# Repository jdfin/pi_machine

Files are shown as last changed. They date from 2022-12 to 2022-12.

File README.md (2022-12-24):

# Pi Machine

Pi Machine prints pi, for as long as you let it run. It was inspired by a couple of projects covered at [Hackaday](https://hackaday.com/): the [Pi Spigot](https://hackaday.com/2021/04/06/raspberry-pi-spigot-puts-digits-of-pi-on-tap/) and [Happy Pi Day 2022](https://hackaday.com/2022/03/15/simple-arduino-build-lets-you-keep-an-eye-on-pi/). The latter's [project page](https://www.linkedin.com/pulse/happy-%25CF%2580-day-2022-cristiano-monteiro) describes how it uses [Xavier Gourdon's](http://numbers.computation.free.fr/Constants/constants.html) [nth-digit algorithm](http://numbers.computation.free.fr/Constants/Algorithms/nthdigit.html) to compute and display digits directly (i.e. compute the nth digit without (necessarily) having computed all the digits before it).

The difference between those and this Pi Machine is that this one prints digits on a thermal printer, and contains logic and hardware (paper-change, power-fail) that in theory lets it run forever. The software herein can be configured to run without any special hardware (other than an Arduino-capable board), but in that case it will just print digits to the serial console.

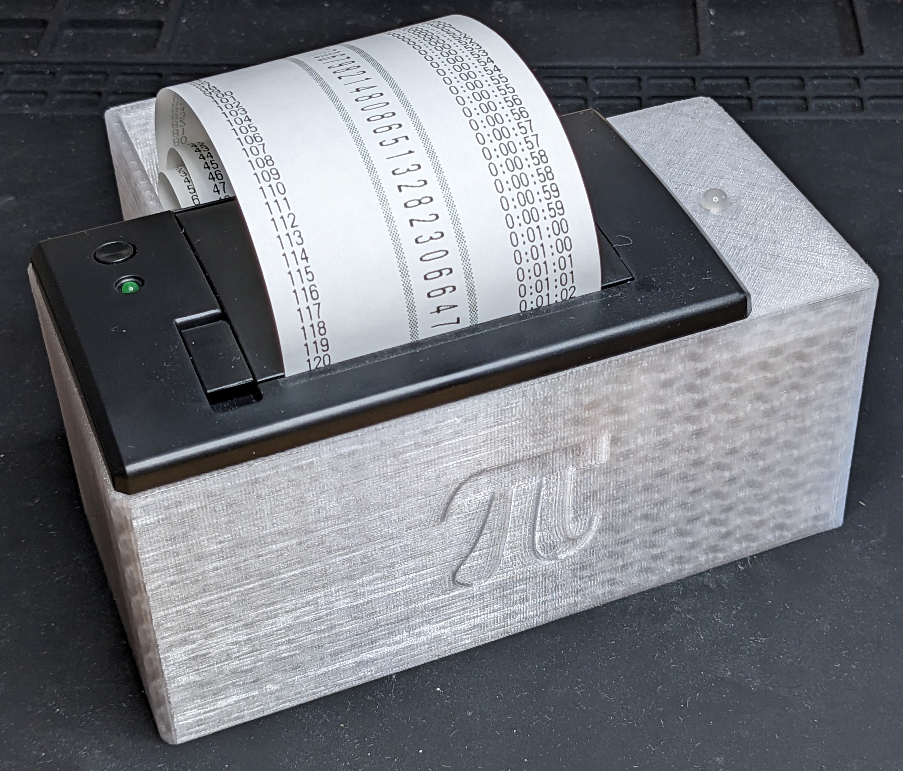
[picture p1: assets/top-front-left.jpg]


The complete (as-built) Pi Machine uses:
* [Adafruit Feather M4 Express](https://www.adafruit.com/product/3857). Minimizing the hardware (how slow can you go) might point to an M0 board, but I had some of the M4 Express "in stock". I first tried on a [DF Robot Beetle](https://www.dfrobot.com/product-1075.html), but that doesn't (easily, out-of-the-box) support 64-bit doubles, and 32-bit doubles lead to a failure at about digit 768, possibly due to the six nines in a row there. It works on an M0 ([Seeeduino XIAO](https://www.seeedstudio.com/Seeeduino-XIAO-Arduino-Microcontroller-SAMD21-Cortex-M0+-p-4426.html) or [Adafruit QT Py - SAMD21](https://www.adafruit.com/product/4600), but I wanted a battery charger, which led me to the [Feather](https://www.adafruit.com/category/943). The [M0 Express](https://www.adafruit.com/product/3403) would be the "lowest-end" hardware, but I had a few of the M4 Express, so the Pi Machine is twice as fast as it could have been. It also runs on a [PJRC Teensy 4.0](https://www.pjrc.com/store/teensy40.html), but 600 MHz and hardware floating point kinda spoils the fun. And I wanted the charger.
* [Thermal Printer](https://www.adafruit.com/product/597). This link is to the printer at Adafruit, but I think you can get the same printer from a number of places. I think the firmware can (will) be different depending on where you get it - I got one of the Adafruit printers via Mouser, and one from Adafruit directly, and they are different in some user-apparent ways. I ended up not using the Adafruit library for it, just because I was innit enough trying to figure it out that I used my own stuff (so the library in here is not suitable for general purpose use). One of the smaller printers would work (after dealing with firmware differences), but the larger paper capacity of the "Mini" seems nice.
* [LiPo](https://www.adafruit.com/product/4236). The purpose of the LiPo is to let you unplug the Pi Machine to move it and not have it start over. I briefly tried making it so it would run from the battery, but it's hard getting enough power to the thermal printer and clean power to the microprocessor such that light printing and brownouts are not an issue. So it charges while plugged in, and when Pi Machine detects it has been unplugged, it just stops printing and waits to be plugged in again. I don't know how long the battery will last. At one point I measured the current draw of just the M4 Express blinking the LED and decided 420 mAh was enough, but don't have or recall the details.
* [RGB LED](https://www.adafruit.com/product/302). This one is has the diffused lens, which I like. I just picked resistors that gave a good brightness, and R, G, and B are just on or off (no pwmmin').
* [Power Jack](https://www.adafruit.com/product/610) and [Power Supply](https://www.adafruit.com/product/276).
* [Switch](https://www.mouser.com/ProductDetail/979-1901.1102). Any switch will do, but this one fits the 3D printed chassis.
* Resistors for power detection (2 x 100K) and the RGB LED (1.5K, 5.1K, 5.1K).
* Connectors for anything you don't want soldered together. The printer is JST-XH (2.5mm), and I used JST-PH (compatible) elsewhere (2.0mm). For the printer I used bits from one of those JST-XH "kits" off Amazon, and for the rest (JST-PH) I use the connectors-with-tails from Adafruit (e.g. [this](https://www.adafruit.com/product/261) and [this](https://www.adafruit.com/product/3814)).
* There is no PCB; the voltage divider fits on the M4 Express, and the LED resistors are hanging in space.

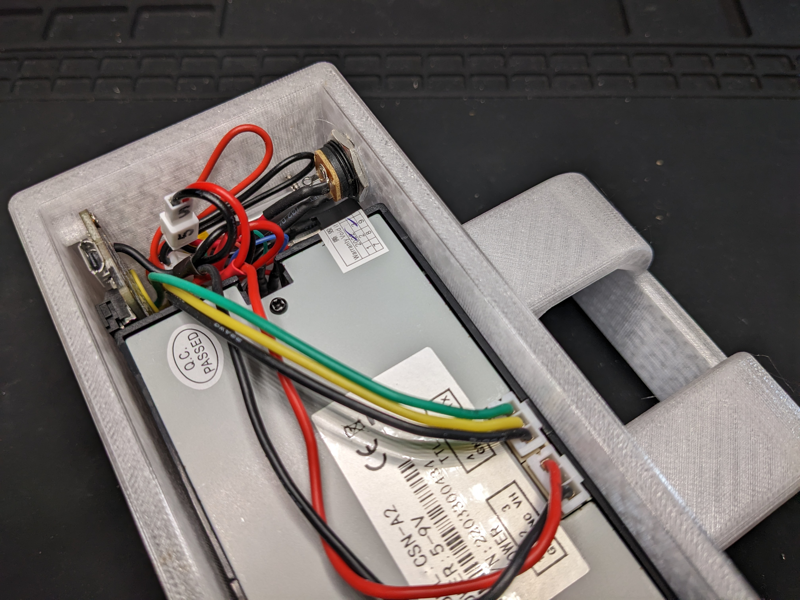
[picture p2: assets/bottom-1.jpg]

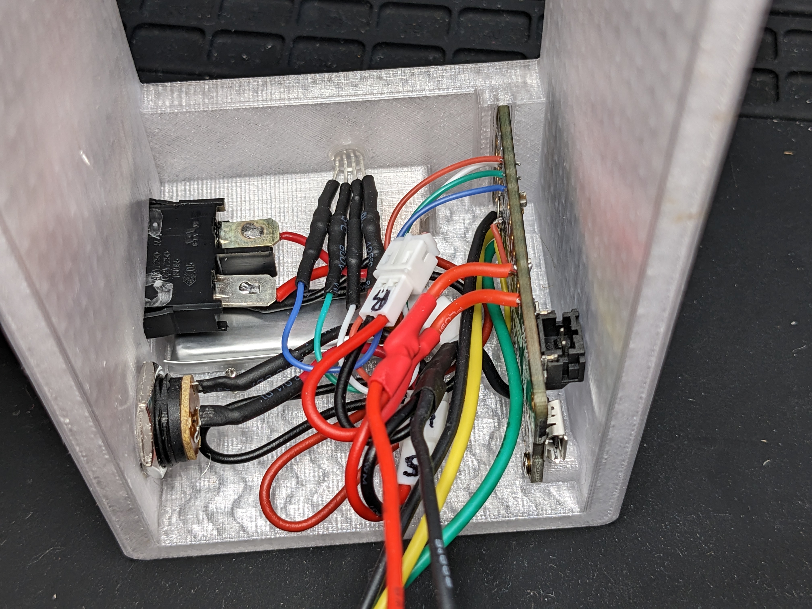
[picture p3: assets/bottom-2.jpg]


## Code

It's all Arduino. I use arduino-cli these days (not the IDE, new or old). You kinda have to know a bit about it already, but here are some bits about how I use it. I use windows, so these are all "cmd.exe" (old-style) batch files. CLI version 0.29 was newest when I did this.
* [Get and install arduino-cli](https://arduino.github.io/arduino-cli/). Drop the executable right there in the "Arduino" directory.
* Edit ac-init.bat according to what you plan to use (it is set for Feather M4 Express as committed). I don't know how to easily find the FQBN for an arbitrary board; running the IDE, enabling verbose output, and plodding through the build output might work.
* Run ac-init.bat. It will get some stuff from Arduino and Adafruit, then create a batch file for the board, namely "ac-feather_m4.bat".
* Run the board batch file. All it does is set an environment variable with the FQBN so the other scripts know how to build/load.
* Run ac-list.bat to look for and list the boards plugged in (so you can see the com port).
* Run ac-build.bat to build and optionally download to the board.
* If needed, run ac-serial.bat to connect to the serial console.

### Running with Only the CPU

No printer, no battery, no power plug. Just a board hanging off USB. This should work with a Feather M4 Express, or with slight modifications to the batch files, an M0 Express, QT Py M0, Xiao, or something of that sort. It just needs 64-bit doubles. It'll compile and run with 32-bit doubles, but the output won't be right.

Edit 2022-11-17_PiMachine.ino:
* WAIT_CONSOLE 1
* PRINT_DIGITS 0
* CHECK_PAPER 0
* CHECK_POWER 0

ac-build 2022-11-17_PiMachine COM*N*

It should build and download.

ac-serial COM*N*

It should connect to the serial port and you should get digit spewage.

### The Software

Stuff shared between sketches is in libraries/PiMachine. That's just how I happen to do it; I can have several test sketches or other variations using the same shared files.
* printer.cpp, printer.h - just enough for this, not for general usage. There might be things in here that don't work in the Adafruit library; I should have fixed and PR'd but didn't. I wouldn't be able to regression test for other firmware versions anyway.
* pidec.cpp, pidec.h - the original source for the nth-digit algorithm, first reformatted (sorry), then converted to run as a subroutine as required for testing and the Pi Machine.
* millis64.cpp, millis64.h - since the idea is to allow it to run for years (ha ha), we need 64 bit milliseconds.
* chrono.cpp, chrono.h - there was a time when I learned and understood std::chrono, and ended up liking it, mostly, iirc. I added this tiny bit of that in response to various subtle problems around pausing and restarting printing (paper change, power unplugged). It's the distinction between time stamps and durations that seems satisfying.
* Sketches - tests for various parts, then the main Pi Machine is in 2022-11-17_PiMachine.
  - Dealing with the printer is split between print_digit() and printer.cpp mentioned previously. Trying to get a digit number, digit, and timestamp on the same line is a little funky, figuring out what that settings mean when text is sideways and such. I think it is the mixing of sideways and not-sideways that causes differences between firmware versions to show up. E.g. one Pi Machine successfully bolds the sideways digit, and one does not.
  
I don't actually understand how the algorithm works, but I've run it to tens of thousands of digits on a Teensy 4.0 and I don't think I've broken it.

### More Hardware

Schematic notes:
* "5V Power Jack" is the 2 amp wall-wart. If this is connected, see POWER NOTE below before plugging in USB or you might be connecting the wal-wart right across your computer's USB port.
* "Switched Battery" is the LiPo, with a switch inline with the + side. The switch is to be able to turn the thing completely off. When running, the switch is normally on so the battery charges. Then when you unplug power, if the switch is on, it sits and waits patiently and does not start all over. If I end up running this thing for a year, I'll probably wish I had put more thought into how the power works.
* 3V3 to the LED comes from the regulator on the Feather. The LED resistors are hanging off the LED, then wired to the CPU board.
* The 100K divider is so the CPU can detect when power is unplugged. It doesn't drop to zero; it drifts down to  3-point-something; enough to detect it. Smaller divider resistors might get it lower, but I did not try. These resistors are mounted to the "Express" area of the CPU board.
* "Printer Serial" is three wires to the JST-XH on the bottom of the printer, and "Printer Power" is two wires going to the other 3-pin JST-XH on the bottom of the printer.

**POWER NOTE:** If the board is powered by a 5V supply you need to **think about** whether you can just plug in USB or not. For the Feather M4 Express, the Pi Machine connects the 5V supply to VUSB, so you should probably not plug in USB at the same time (lest your computer and the wall-wart argue over who can supply more current). I have a USB cable where I cut the +5 wire just for this purpose; you can power with the wall-wart, and plug in the USB cable that just has D+, D-, and GND, and it works nicely.

The chassis was all done in Fusion 360 and printed on a Prusa i3 MK3S+ with PETG.

## Tiny Pi Machine

My grandson likes to push buttons and make things whirr, so I built the Tiny Pi Machine with the "[Nano](https://www.adafruit.com/product/2752)" printer that I ended up not using for the Pi Machine. It does not compute pi; it just prints it as long as the button is down, then starts over and does it again the next time you push the button. Not terribly exciting unless you are 3; then it's easy to go through rolls and rolls of paper.

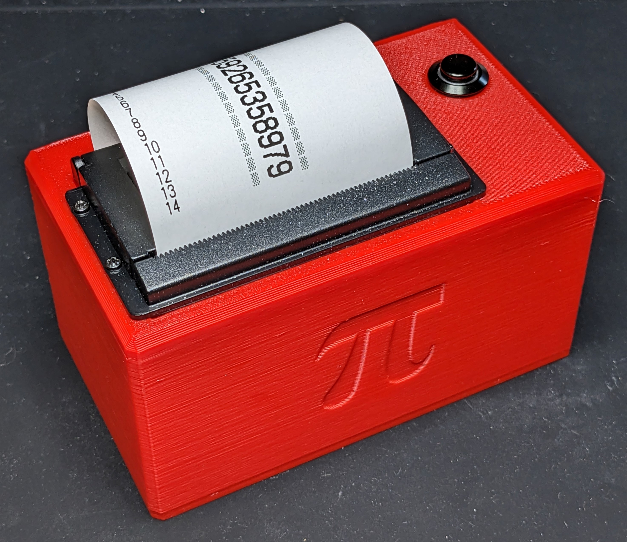
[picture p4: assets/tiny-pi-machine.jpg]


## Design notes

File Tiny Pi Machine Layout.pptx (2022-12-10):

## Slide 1

VIN

B+

ON

VOUT

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
VOUT

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
CTRL

A0

A1

A2

5V

TOP

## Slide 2

VIN

B+

ON

VOUT

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
VOUT

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
CTRL

A0

A1

A2

5V

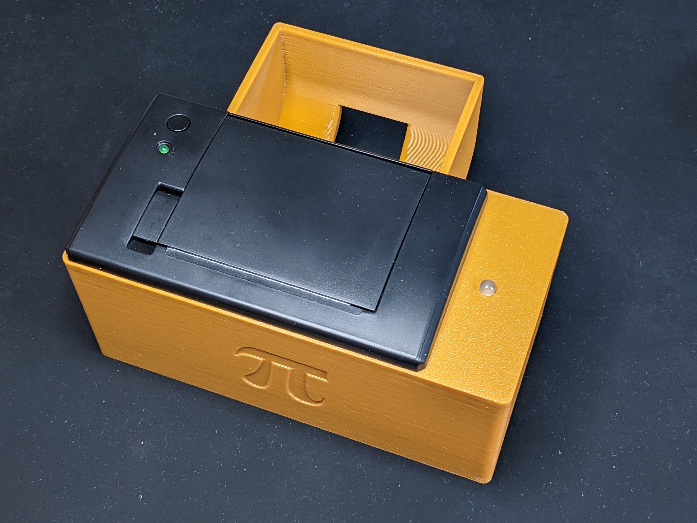
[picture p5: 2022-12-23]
assets/top-front-right.jpg

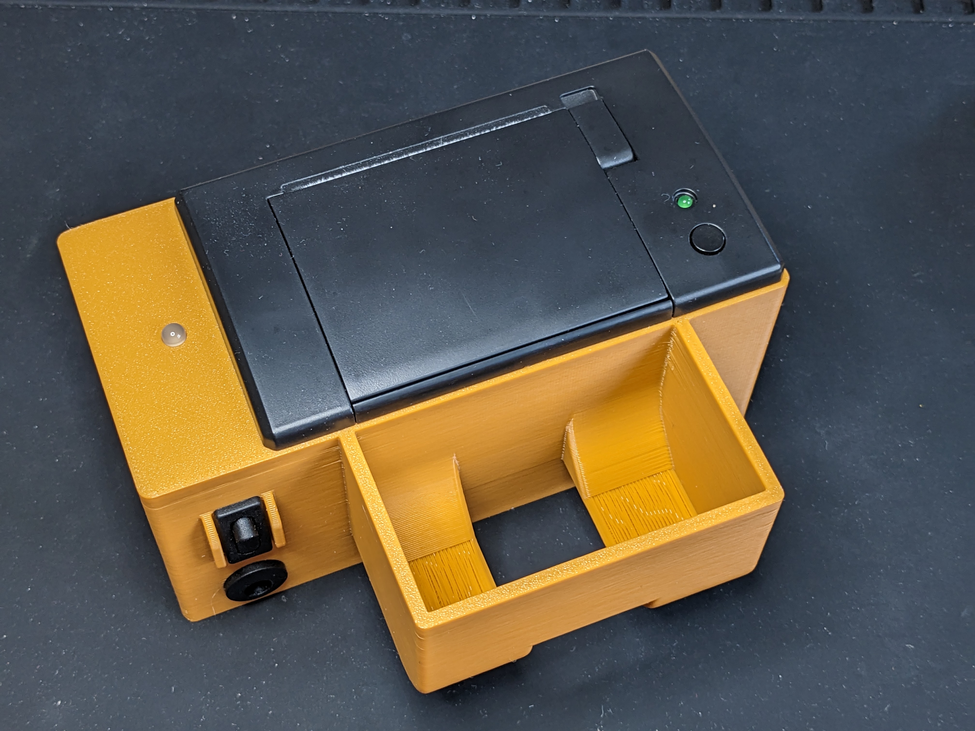
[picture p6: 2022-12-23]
assets/top-rear.jpg

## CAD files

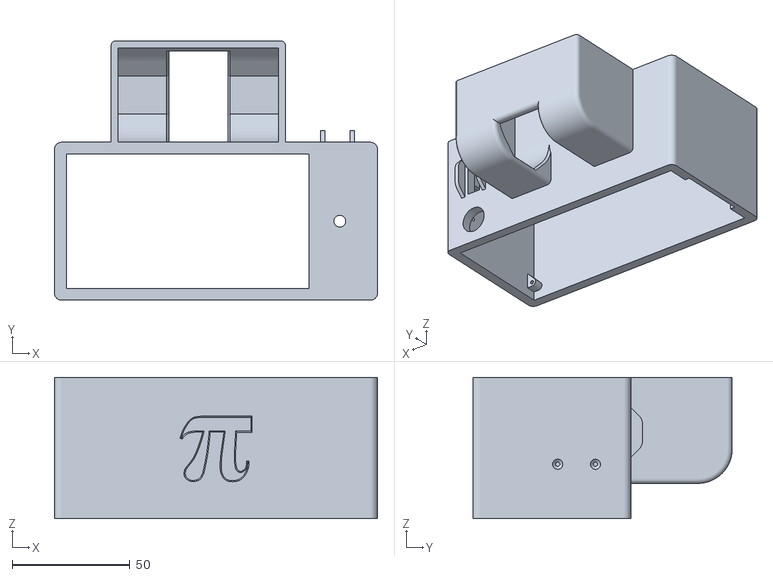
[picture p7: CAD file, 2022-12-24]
pi_machine.stl
137.0 x 110.0 x 60.0

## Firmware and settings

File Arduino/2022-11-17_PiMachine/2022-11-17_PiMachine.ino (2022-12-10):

// PiMachine

#include <Arduino.h>
#include <string.h>
#include <stdio.h>
#include <pidec.h>
#include <rgb.h>
#include <printer.h>
#include <chrono.h>

// if 1, wait for serial (usb) console before starting
#define WAIT_CONSOLE 0

// if 1, print to real printer in addition to console
#define PRINT_DIGITS 1

// if 1, check for paper out (can do this without printing digits)
#define CHECK_PAPER 1

// if 1, switch on GPIO simulates paper out
#define CHECK_PAPER_FAKE 0

static const int paper_fake_pin = 10;
static const int paper_fake_yes = 1; // gpio when "paper is present"

// if 1, check power and pause when not present
// (requires divider connected to a/d pin)
#define CHECK_POWER 1

// Minimum number of milliseconds per digit printed.
// 250 seems to be about the fastest, slower for debugging.
#if PRINT_DIGITS
static const Interval print_interval(500);
#else
static const Interval print_interval(0);
#endif

// 19200 for the Mini, 9600 for the Nano
static const int printer_baud = 19200;

static Printer printer(Serial1);

static const int red_pin = 5;
static const int green_pin = 6;
static const int blue_pin = 9;
static Rgb led(red_pin, green_pin, blue_pin);


// The start time is advanced when waiting for power or paper.
static Time start_time;

// In the program, first digit after the decimal (the 1) is digit zero
// (that is dictated by DigitsOfPi).
//
// In the printout, the initial '3' is digit zero, so the printout uses
// digit_num + 1.
//
// digit_num: -4 and -3 are spaces, -2 is the '3', -1 is the '.', then
//            0.. are the digits after the decimal point
static const int32_t digit_num_start = -4;
static int32_t digit_num = digit_num_start;


// How long it took to calculate the most recent digit.
// loop() sets this and print_digit() uses it.
static Interval digit_interval;


#if CHECK_PAPER || CHECK_PAPER_FAKE

// return true if the printer claims to have paper, false otherwise
static bool check_paper()
{
#if CHECK_PAPER_FAKE
  return (digitalRead(paper_fake_pin) == paper_fake_yes);
#else
  return printer.paper();
#endif
}

#endif // CHECK_PAPER || CHECK_PAPER_FAKE


// If paper is detected, return true immediately.
// If paper is not detected, wait for it to be detected continuously
// for 10 seconds, then return false.
// Logic is similar to power_wait, but in here we also allow for power
// disappearing (i.e. run out of paper, unplug it to move it or something).
static bool paper_wait()
{

#if CHECK_PAPER || CHECK_PAPER_FAKE

  if (check_paper())
    return true;

  Serial.println("paper out");

  // Time we started waiting for more paper. This is used to adjust the global
  // start_time so it doesn't include paper-out time.
  const Time wait_start;

  // Need to see paper for 10 seconds before continuing.
  const Interval wait_timeout(10000);

  // Last time paper was detected as "out".
  Time paper_out;

  while ((Time::now() - paper_out) < wait_timeout) {

    if (!power_wait()) {
      // power went away, then came back
      paper_out = Time::now();
    }

    if (check_paper()) {
      // solid red means we see paper, waiting for 10 seconds
      led.set(Rgb::Red);
    } else {
      // winking red means we don't see paper
      led.pattern(Rgb::Red, 10, Rgb::Off, 990);
      paper_out = Time::now();
    }

    led.loop(); // handle blinking

    yield(); // could be in this while loop for a long time

  } // while

  // Adjust start_time as if we didn't have to wait.
  start_time += (Time::now() - wait_start);

  // Back up 30 digits after paper out. A nice clean end-of-paper only needs
  // a few digits of backing up (4 or 5 might do), but sometimes the end of
  // the roll is folded back on itself and a couple of inches at the end
  // don't print because it's trying to print on the back of the paper.
  // We're printing about 8.5 lines per inch.
  digit_num -= 30;
  if (digit_num < digit_num_start)
    digit_num = digit_num_start;

  Serial.println("paper okay");

  return false;

#else // CHECK_PAPER(_FAKE)

  return true;

#endif // CHECK_PAPER(_FAKE)

} // paper_wait


// return true if 5V supply is present, false otherwise
static bool check_power()
{

#if CHECK_POWER

  // VUSB is 5.0V when plugged in, and is about 3.3V when not plugged in.
  // The pin is half that. Set threshold for halfway between 5.0 and 3.3.
  // Halfway between 3.3 and 5.0 is 4.15V.
  // Pin is half that, or 2.075V.
  // ADC reading is 1024 at 3.3V, so ADC threshold is 644.
  const int v_thresh = 644;
  int v = analogRead(2);

  return (v >= v_thresh);

#else // CHECK_POWER

  return true;

#endif // CHECK_POWER

} // check_power


static bool power_wait()
{

  if (check_power())
    return true;

  Serial.println("power out");

  // Wait to be plugged in for at least 1 sec, then return false.
  // The delay is to let the printer boot up.
  // Returning false prevents the just-calculated digit from being printed.

  const Time wait_start;

  const Interval wait_timeout(1000); // 1 second

  // last time power was seen low
  Time power_low;

  while ((Time::now() - power_low) < wait_timeout) {

    if (check_power()) {
      // solid blue means we see 5V power, waiting 1 second
      led.set(Rgb::Blue);
    } else {
      // winking blue means we don't see 5V power
      led.pattern(Rgb::Blue, 10, Rgb::Off, 990);
      power_low = Time::now();
    }

    led.loop(); // handle blinking

    yield(); // could be in this while loop for hours

  } // while

  // Adjust start_time as if we didn't have to wait.
  start_time += (Time::now() - wait_start);

  // Back up three digits after power outage; really only the previous one
  // might be chopped off, but maybe there's some other case where more than
  // one might be lost, and losing a digit would be most terrible.
  digit_num -= 3;
  if (digit_num < digit_num_start)
    digit_num = digit_num_start;

  Serial.println("power okay");

  return false;

} // power_wait


// print a digit (paper and power already checked)
// 
static void print_digit(char digit)
{
  // Limit print rate so we don't queue up lines in the receive buffer,
  // which breaks paper-out handling. This is different from worrying
  // about overrunning the receive buffer; we basically want to know a
  // digit is on the paper before we try to print another one.
  static Time last_print_time;
  while ((Time::now() - last_print_time) < print_interval)
    delay(1);
  last_print_time = Time::now();

  // timestamp that will print with digit
  uint32_t h, m, s, ms;
  (last_print_time - start_time).hmsm(h, m, s, ms);

  // digit number to print
  int32_t pr_digit_num;
  if (digit_num == -2)
    pr_digit_num = 0; // initial '3'
  else
    pr_digit_num = digit_num + 1;

  // large font is 12 pixels wide x 24 pixels high

  // rotated and doubled digit is 48 pixels wide
  // digit should be centered on 384/2 = 192, so should print at
  // 192 - (48 / 2) = 168

  // line will be:
  // digit number: 12 chars @ 12 pixels = 144 pixels
  // border:        2 chars @ 12 pixels =  24 pixels
  // digit:         1 char  @ 48 pixels =  48 pixels
  // border:        2 chars @ 12 pixels =  24 pixels
  // timestamp:    12 chars @ 12 pixels = 144 pixels
  // total:                               384 pixels

  char buf[50];

  // only print number and timestamp if digit is 0..9
  if ('0' <= digit && digit <= '9')
    sprintf(buf, "%-12ld| %c |%6lu:%02lu:%02lu", pr_digit_num, digit, h, m, s);
  else
    sprintf(buf, "            | %c |            ", digit);
  Serial.print(buf);

  sprintf(buf, "%9lld", digit_interval.ms());
  Serial.print(buf);

  Serial.println();

#if PRINT_DIGITS

  // digit number
  if ('0' <= digit && digit <= '9')
    sprintf(buf, "%-12ld", pr_digit_num); // 12 chars left-justified
  else
    strcpy(buf, "            "); // 12 chars

  printer.rotate(false);
  printer.mode(Printer::Modes::FontLarge);
  printer.print(buf);
  printer.print(0xb2); // gray box
  printer.print(' ');

  // digit
  printer.rotate(true);
  printer.mode(Printer::Modes::FontLarge | Printer::Modes::BoldOn |
               Printer::Modes::Height2x | Printer::Modes::Width2x);
  printer.print(digit);

  // Timestamp. This will run up against the digit in 11 years, then
  // do something uglier in 114 years.
  printer.rotate(false);
  printer.mode(Printer::Modes::FontLarge);
  printer.print(' ');
  printer.print(0xb2); // gray box
  if ('0' <= digit && digit <= '9') {
    sprintf(buf, "%6lu:%02lu:%02lu", h, m, s); // 12 chars right-justified
    printer.print(buf);
  }

  printer.line_space(0);  // lines as close together as possible
  printer.flush();        // print buffered data and advance paper

  printer.mode(); // defaults

#endif // PRINT_DIGITS

} // print_digit


void setup()
{
  led.begin();

  led.set(Rgb::White);

  Serial.begin(115200);

#if WAIT_CONSOLE
  while (!Serial)
    ;
  delay(250);
#endif

#if CHECK_PAPER_FAKE

  // switch from gpio to ground
  // open is paper-yes, closed is paper-no
  pinMode(paper_fake_pin, INPUT_PULLUP);

#endif

  // printer.begin() sets the baud rate and sends a reset command,
  // but does not wait for any responses from the printer
  printer.begin(printer_baud);
  delay(250);

  start_time = Time::now();

  digit_num = digit_num_start;

} // setup


// Algorithm will only works starting at (approximately) digit 50 after
// the decimal (I don't know why) so before that we cheat and look it up
// This also puts a couple of blank lines at the start, and prints the
// decimal point.
static const char *pi50 =
    "  3.1415926535897932384626433832795028841971693993751058209";


void loop()
{
  led.set(Rgb::Green);

  Time digit_start_time;

  char digit_char;

  if (digit_num < 50) {

    // digit_num == 0 should get the '1' after the decimal point (pi50[4])
    // digit_num starts at -4

    digit_char = pi50[digit_num + 4];

  } else {

    double x = DigitsOfPi(digit_num);
    double y = x * 1.0e9;
    int digit = int32_t(y) / 100000000;

    digit_char = '0' + digit;

  }

  // how long it took to calculate this digit (only used for serial prints)
  digit_interval = Time::now() - digit_start_time;

  // If power_wait() returns false, power was detected as gone, then we
  // waited for it to come back. The last line printed might be faint or
  // chopped off, so digit_num has been backed up and we need to go back
  // and recalculate a previous digit.

  if (!power_wait())
    return;

  // Similar to power_wait(); start over on a previous digit. This backs up
  // farther than power_wait since the end of the paper can cause loss of more
  // digits.

  if (!paper_wait())
    return;

  print_digit(digit_char);
  digit_num++;

} // loop

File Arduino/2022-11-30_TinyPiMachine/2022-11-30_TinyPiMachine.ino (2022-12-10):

// TinyPiMachine

// While the button is pressed, print digits of pi. When the button has been
// released for 1 second, print some blank lines and power off.

#include <Arduino.h>
#include <string.h>
#include <stdio.h>
#include <printer.h>
#include <tiny_pi_machine.h>
#include "pi.h"

// if 1, wait for serial (usb) console before starting
#define WAIT_CONSOLE 0

// if 1, print to real printer in addition to console
#define USE_PRINTER 1

// Minimum number of milliseconds per digit printed.
// 250 seems to be about the fastest, slower for effect (or debugging).
static const uint32_t print_interval_ms = 500;

// Below this, print recharge message and stop.
// See comments at printer.heat() call in setup().
static const uint32_t battery_min_mv = 3800;

static Printer printer(Serial1);

static int32_t digit_num = 0;

// for snprintf
static const int pbuf_len = 40;
static char pbuf[pbuf_len];


// Check button each call. When it has been seen released for btn_timeout_ms,
// print some lines, delay, then power off (never returns in that case).
static void check_button()
{
  static const uint32_t btn_timeout_ms = 500;
  static uint32_t last_ms = millis();

  int btn = digitalRead(gpio_btn);
  if (btn == 1)
    last_ms = millis();

  if ((millis() - last_ms) >= btn_timeout_ms) {

#if USE_PRINTER
    for (int i = 0; i < 5; i++)
      printer.print('\n');
#endif

    // delay to (maybe) finish printing a digit and scroll the blank lines
    delay(1000);

    // Power off. Is there a race condition where the button is pressed again
    // just as we try to power off? Maybe? Put the power off in a loop in case.
    while (true) {
      digitalWrite(gpio_off, 1);
      delay(1);
    }
  }
}


// Check battery. Called once at startup. If battery is below battery_min_mv,
// print a message and power off.
static void check_battery()
{
  int adc = analogRead(adc_batt);
  int mv = (adc * 625L + 64) / 128; // 64 is for rounding

  if (mv >= battery_min_mv) {

#if 0
    snprintf(pbuf, pbuf_len-1, "Battery: %d mV", mv); // 23 chars max
    Serial.println(pbuf);
#if USE_PRINTER
    printer.print(pbuf);
#endif
#endif

    return;
  }

  // does not return

  snprintf(pbuf, pbuf_len-1, "CHARGE BATTERY (%d mV)", mv); // 31 chars max

  Serial.println(pbuf);

#if USE_PRINTER
  printer.print(pbuf);
  for (int i = 0; i < 5; i++)
    printer.print('\n');
#endif

  // let the printer print, and maybe allow connecting debugger
  delay(2000);
  while (true) {
    digitalWrite(gpio_off, 1);
    delay(1);
  }

} // check_battery


// print a digit
static void print_digit(char digit)
{
  check_button();

  // Limit print rate so we don't queue up lines in the receive buffer,
  // which breaks paper-out handling. This is different from worrying
  // about overrunning the receive buffer; we basically want to know a
  // digit is on the paper before we try to print another one.
  static uint32_t last_print_ms = millis();
  while ((millis() - last_print_ms) < print_interval_ms)
    delay(1);
  last_print_ms = millis();

  // large font is 12 pixels wide x 24 pixels high

  // rotated and doubled digit is 48 pixels wide
  // digit should be centered on 384/2 = 192, so should print at
  // 192 - (48 / 2) = 168

  // line will be:
  // digit number: 12 chars @ 12 pixels = 144 pixels
  // border:        2 chars @ 12 pixels =  24 pixels
  // digit:         1 char  @ 48 pixels =  48 pixels
  // border:        2 chars @ 12 pixels =  24 pixels
  // nothing:      12 chars @ 12 pixels = 144 pixels
  // total:                               384 pixels

  // only print number if digit is 0..9
  if ('0' <= digit && digit <= '9')
    snprintf(pbuf, pbuf_len-1, "%-12ld| %c |", digit_num, digit); // 18 chars
  else
    snprintf(pbuf, pbuf_len-1, "            | %c |", digit); // 18 chars
  pbuf[pbuf_len-1] = '\0';

  Serial.println(pbuf);

#if USE_PRINTER

  // digit number
  if ('0' <= digit && digit <= '9')
    snprintf(pbuf, pbuf_len-1, "%-12ld", digit_num); // 13 chars
  else
    strncpy(pbuf, "            ", pbuf_len-1); // 13 chars
  pbuf[pbuf_len-1] = '\0';

  printer.rotate(false);
  printer.mode(Printer::Modes::FontLarge);
  printer.print(pbuf);
  printer.print(0xb2); // gray box
  printer.print(' ');

  // digit
  printer.rotate(true);
  printer.mode(Printer::Modes::FontLarge | Printer::Modes::BoldOn |
               Printer::Modes::Height2x | Printer::Modes::Width2x);
  printer.print(digit);

  printer.rotate(false);
  printer.mode(Printer::Modes::FontLarge);
  printer.print(' ');
  printer.print(0xb2); // gray box

  printer.line_space(0);  // lines as close together as possible
  printer.flush();        // print buffered data and advance paper

  printer.mode(); // defaults

#endif // USE_PRINTER

} // print_digit


void setup()
{
  Serial.begin(115200);

  pinMode(gpio_btn, INPUT);

  // do not glitch high
  digitalWrite(gpio_off, 0);
  pinMode(gpio_off, OUTPUT);

#if WAIT_CONSOLE
  while (!Serial)
    ;
  delay(250);
#endif

  // printer.begin() sets the baud rate and sends a reset command,
  // but does not wait for any responses from the printer
  printer.begin(printer_baud);
  delay(500);

  // This intertwines with the minimum allowed battery voltage. The more
  // current the printer pulls, the higher the threshold has to be. When the
  // printer prints a line, the voltage from the battery dips (due to IR of
  // the battery) and can hit the battery protection cutoff. With (5, 200, 1),
  // the drain test program works to around a measured voltage of 3.6 V.
  // Presumably, as the battery ages, the IR (and drop) will be greater.
  printer.heat(5, 200, 1);

  check_battery(); // doesn't return if battery too low

} // setup


void loop()
{
  if (digit_num < pi_len) {
    print_digit(pgm_read_byte(pi + digit_num));
    if (digit_num == 0) {
      print_digit('.');
    }
    digit_num++;
  } else if (digit_num == pi_len) {
    Serial.println("No more pi!");
#if USE_PRINTER
    printer.print("No more pi!\n");
#endif
    digit_num++;
  } else {
    // digit_num just sits at pi_len+1 forever
  }
}

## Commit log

2022-11-17 original pi spigot algorithm
    Algorithm from: http://numbers.computation.free.fr/Constants/constants.html
    On left side, "Algorithms"
    Then "N-th digit computation"
    Then 75% of the way down, "source code" brings up the code in a frame
    Copied it, changed line endings to "unix", committed.
2022-11-17 added basic printer support and test/demo
    Just enough printer support. Adafruit printer is missing a
    thing or two (like rotate), paper detection doesn't seem to
    work on nano, and there's a ton of code not needed (including
    the timing stuff). This is just enough.
    Test/demo program prints like the pi machine will use it.
2022-11-17 added PiMachine
    No known problems. Handles paper-out by waiting, then repeating
    the last two digits. Relies on Mini Thermal Printer indicator to
    say when paper is out (it does a three-blink pattern).
    [2022-11-17_PiMachine.ino]
2022-11-17 added arduino-cli batch files
2022-11-22 added rgb.h (simple RGB LED class)
2022-11-22 added RGB LED, power check, added build variants
    RGB LED on three GPIOS. Check for 5V power via resistor divider to
    ADC. Build variants to aid in testing: PRINT_DIGITS, CHECK_PAPER,
    WAIT_CONSOLE, CHECK_POWER.
2022-11-22 simple test for power present/not present
    Read and report voltage on ADC, presumably 5V / 2. Requires a
    hacked USB cable that does not connect 5V power (so you can see
    serial output while disconnecting 5V power).
2022-11-23 added patterns to LED class
2022-11-26 64-bit millis, reworked paper/power
    PiMachine: reworked how paper-out and power-out detection and
    recovery works.
    PiMachine: keep track of 64 milliseconds. There's still some case
    in paper-out and/or power-out where it goes negative.
    Added millis64() and test sketch.
    Bugfixes:
    Rgb::pattern() correctly checks that the same pattern is already
    running before deciding not to do anything.
    Printer::status() waits up to 100 msec (was 30 msec) for a response.
    30 msec is not enough. Did not look further to see exactly how long
    is long enough.
    [2022-11-17_PiMachine.ino, 2022-11-25_Millis64Test.ino]
2022-12-10 added Printer::heat()
    Mainly to support Tiny Pi Machine running on a battery, where one
    must slow the printing to reduce peak current draw.
2022-12-11 added PrinterTest
    More of a print demo program. Used it to show that two different
    printers with different firmwares produce different output (one
    does not embolden double-sized rotated characters). Oh well.
2022-12-24 added stl file
    Pi Machine v19
    [pi_machine.stl]
